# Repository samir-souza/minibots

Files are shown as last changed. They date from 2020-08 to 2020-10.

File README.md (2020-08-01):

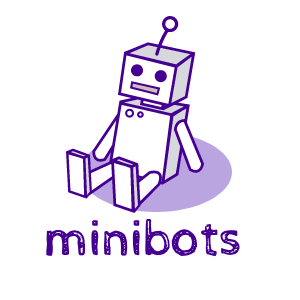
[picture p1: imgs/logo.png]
<br> 

**minibots** is an open source and open hardware platform for experimenting with autonomous bots, Machine Learning and Programming. You can download the code and the assets to create your own fleet of bots, using a 3D printer and some basic electronic components. It is based on the ESP8266 uController, but you can modify it and use any uController you want. 
 
<br><br> 

<p align="center">
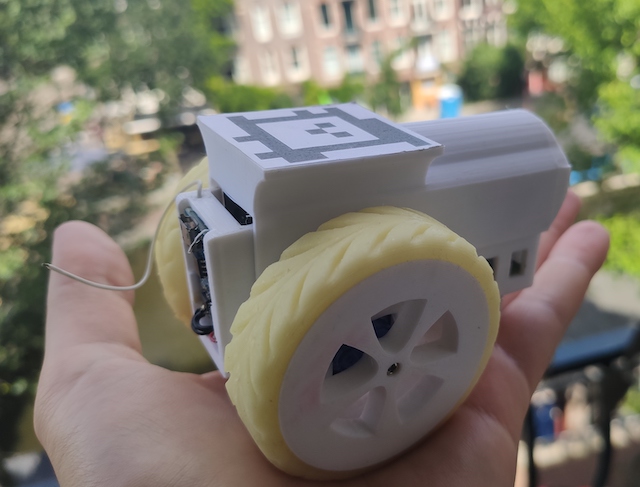
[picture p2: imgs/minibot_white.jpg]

</p>

## Smart City with minibots
In this repo you will find a demo of a Smart City simulation. The idea of this demo is to use **minibots** to 
represent cars moving around on the streets of a city. There are a few places around the track like: houses, gas stations, buildings, etc.
The cars are going from on place to another, simulating a rush hour and generting traffic jams. The targets are selected randomly, and
each car automatically selects the next random target as soon as it gets to the current target place. The controller will try to 
re-route the cars to alternative paths to alleviate the traffic. You can also make the things worse by manually adding some 
obstacles to the streets, like: dogs, pedestriang, etc.
Also, there is a special marker that you can put close to a place. It will bias the next target selected by the first car that finishes the current path.  

<p align="center">
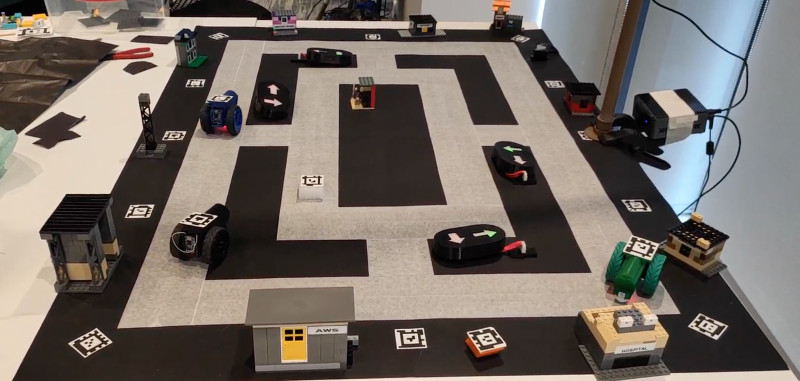
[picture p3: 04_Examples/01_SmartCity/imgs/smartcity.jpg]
 
</p> 

[Click here for more details about this demo](04_Examples/01_SmartCity)

## Components

A Minibot is composed by three modules: 1) the 3D printed parts and a few other parts; 2) the bot Printed Circuit Board (PCB); and 3) the firmware;

### 3D Models
In the first module [3D Models](01_3DModels) you will find the STL files and the FreeCAD projects used to build this project. Just follow the instructions on the module page "[3D Models](01_3DModels)" to get the files and print them.
### Bot PCB
In the second module [Bot PCB](02_BotPCB) you will find instructions about how to create the Printed Circuit Board for your Minibot. Also, you'll find the [Gerber files](https://en.wikipedia.org/wiki/Gerber_format), required for manufacturing the PCB and the components list.
### Firmware
In the third module [Firmware](03_BotFirmware) you will find the binary images and a Dockerfile that you can use to hack and customize the firmware of your Minibot. The firmware is for the uController ESP8266 and is based on Nodemcu LUA: https://nodemcu.readthedocs.io/en/master/. So, after installing the Nodemcu firmware you can customize the Lua scripts to adapt your Minibot to any project.

## Assembling
Click on [ASSEMBLING](ASSEMBLING.md) to see the instructions of how to create your own Minibot from scratch.

# License
The 3D Models and the PCB projects are released in Creative Commons Attribution-ShareAlike 4.0 License and the source code available in this repository is licensed under the GNU General Public License v3.0.

----
<div>Logo created by <a href="https://www.designevo.com/logo-maker/" title="Free Online Logo Maker">DesignEvo logo maker</a></div>

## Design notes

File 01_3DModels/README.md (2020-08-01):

## 3D Printing some parts for your Minibot

Here you will find all the parts you need to print in order to assembly your Minibot. Print the followint itens and prepare the [Printed Circuit Board - PCB](/02_BotPCB) to assemble your Minibot:

 - [Chassis](stl/01_Chassis.stl)
 - [Wheel (x2)](stl/02_Wheel.stl)
 - [Cover Shell](stl/21_MinibotShell.stl)
 - PCB Cover: Depending on the size of your servo (yes, it varies a lot from vendor to vendor), choose: [Big](stl/04_PCBCoverBig.stl) or [Small](stl/05_PCBCoverNormal.stl)

<table>
  <tr>
    <td align="center">Wheels</td>
    <td align="center">PCB with servos</td>
    <td align="center">Chassis cover</td>
    <td align="center">Wheels installed</td>
  </tr>
  <tr>
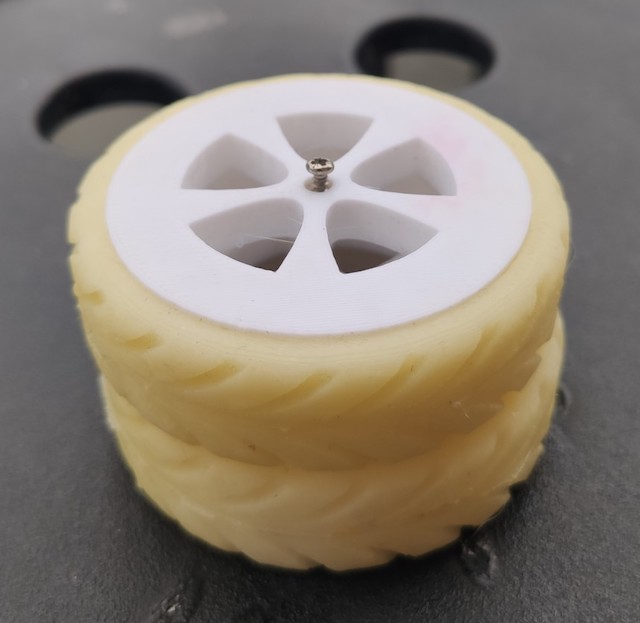
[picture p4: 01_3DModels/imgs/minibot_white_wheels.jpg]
    <td align="center"></td>
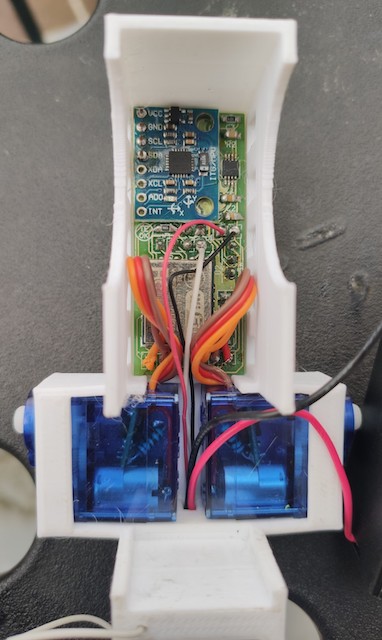
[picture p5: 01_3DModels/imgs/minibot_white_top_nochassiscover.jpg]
    <td align="center"></td>
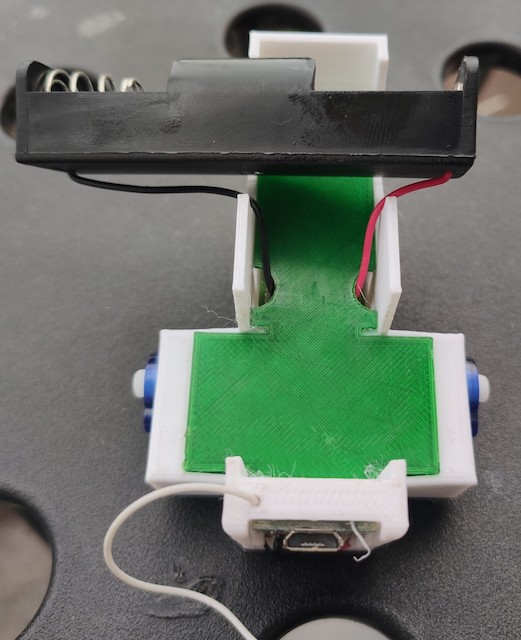
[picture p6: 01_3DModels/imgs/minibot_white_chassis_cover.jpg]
    <td align="center"></td>
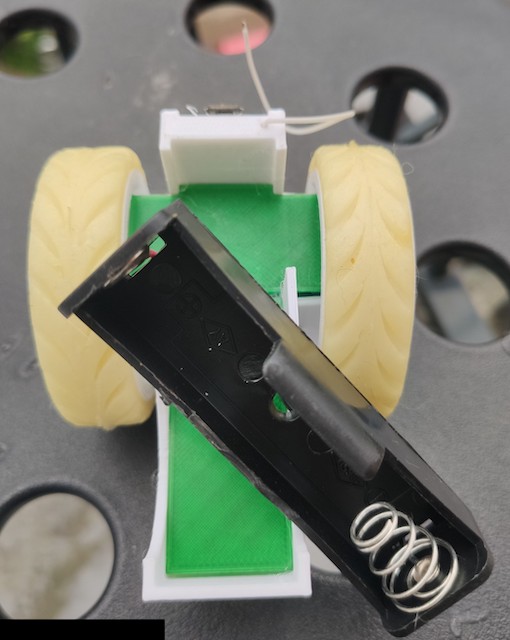
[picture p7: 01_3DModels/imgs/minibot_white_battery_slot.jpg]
    <td align="center"></td>    
  </tr>
  <tr>
    <td align="center">Without shell - battery slot</td>
    <td align="center">Top vision with shell</td>
    <td align="center">Rear view - battery recharger</td>
    <td align="center">Bottom view</td>
  </tr>
  <tr>
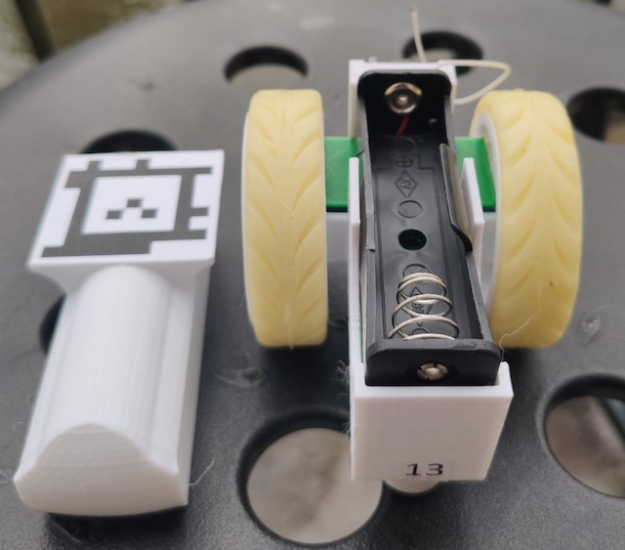
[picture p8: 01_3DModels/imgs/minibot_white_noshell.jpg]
    <td align="center"></td>    
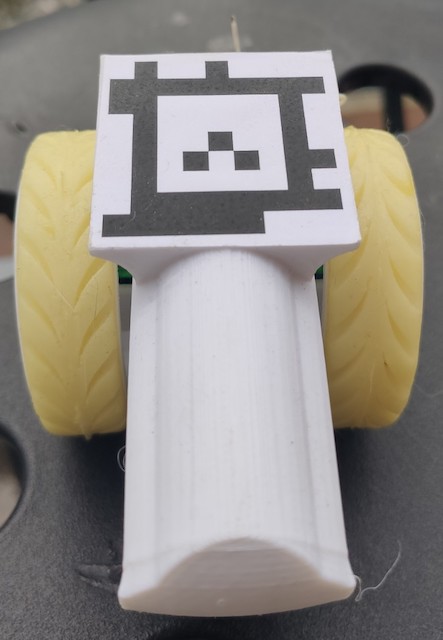
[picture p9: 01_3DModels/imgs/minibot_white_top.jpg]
    <td align="center"></td>
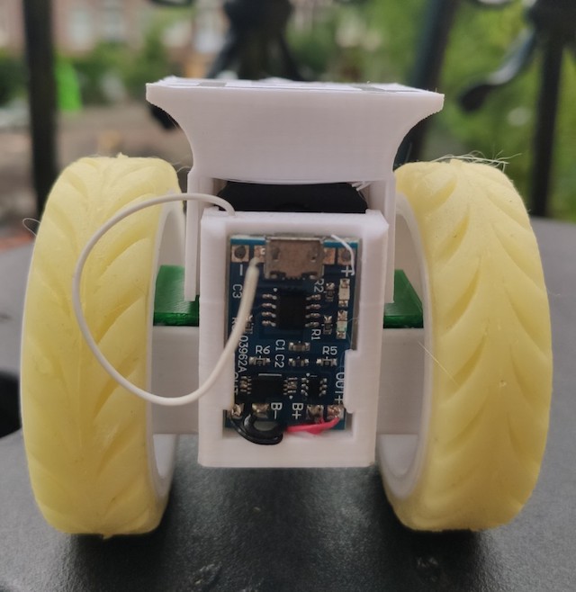
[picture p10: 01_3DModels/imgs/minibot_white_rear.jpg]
    <td align="center"></td>
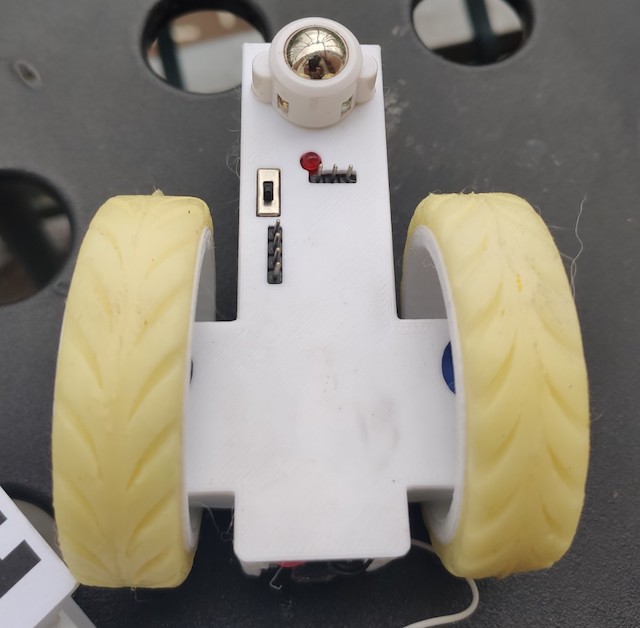
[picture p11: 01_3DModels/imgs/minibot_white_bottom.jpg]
    <td align="center"></td>
  </tr>
</table>

## Preparing the tyres
You can make tyres for your Minibot with Silicon and Cornstarch! :) Yeah, that's it. To do that, you just need to 3D print the mold:
 - [Mold part A](stl/32_TyreModePartA.stl)
 - [Mold part B](stl/33_TyreModldPartB.stl)
 
Then you just need to prepare the silicon the way it is explained here in this video: https://www.youtube.com/watch?v=u9VzjrzLDiE&pbjreload=101

Put the silicone in both parts of the mold, close it tightly and wait for ~2hs before opening it. Keep in mind the the cure time for this formula is something like 24hs. So, don't stretch or try to put it in the wheel before that time. IMO you achieve better by letting the tyres to cure for 48hs.

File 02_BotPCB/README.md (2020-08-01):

## Preparing the PCB

Minibots is based on a very popular and cheap uController, the ESP8266. So, the PCB is basically this uController connected to two servos (controlled by PWM) and other elements, like the classic accelerometer+gyroscope MPU6050, external pins, control LED, etc.

The PCB was created with KiCad **v4.0.2+dfsg1-stable** and you can see the KiCad project in this directory. The Gerber files can also be found in this dir. In order to manufacture a new PCB for you Minibot, you can use the Gerber files. If you never created a PCB before, you can use some online services that you just upload the Gerber files, pay for the boards and you then receive the boards at your home. The project is very simple. It has just one layer and you can make tracks with **copper 2Oz**.

<table>
  <tr>
    <td>PCB Layout</td>
    <td>Connections</td>
    <td>Top</td>
    <td>Bottom</td>
  </tr>
  <tr>
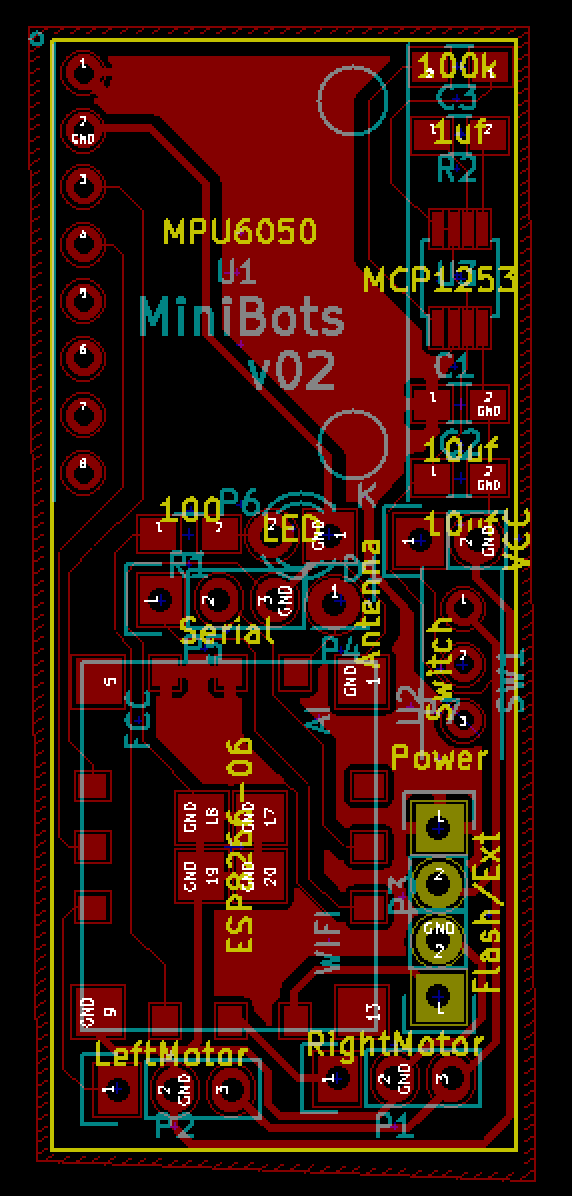
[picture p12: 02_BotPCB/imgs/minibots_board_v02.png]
    <td></td>
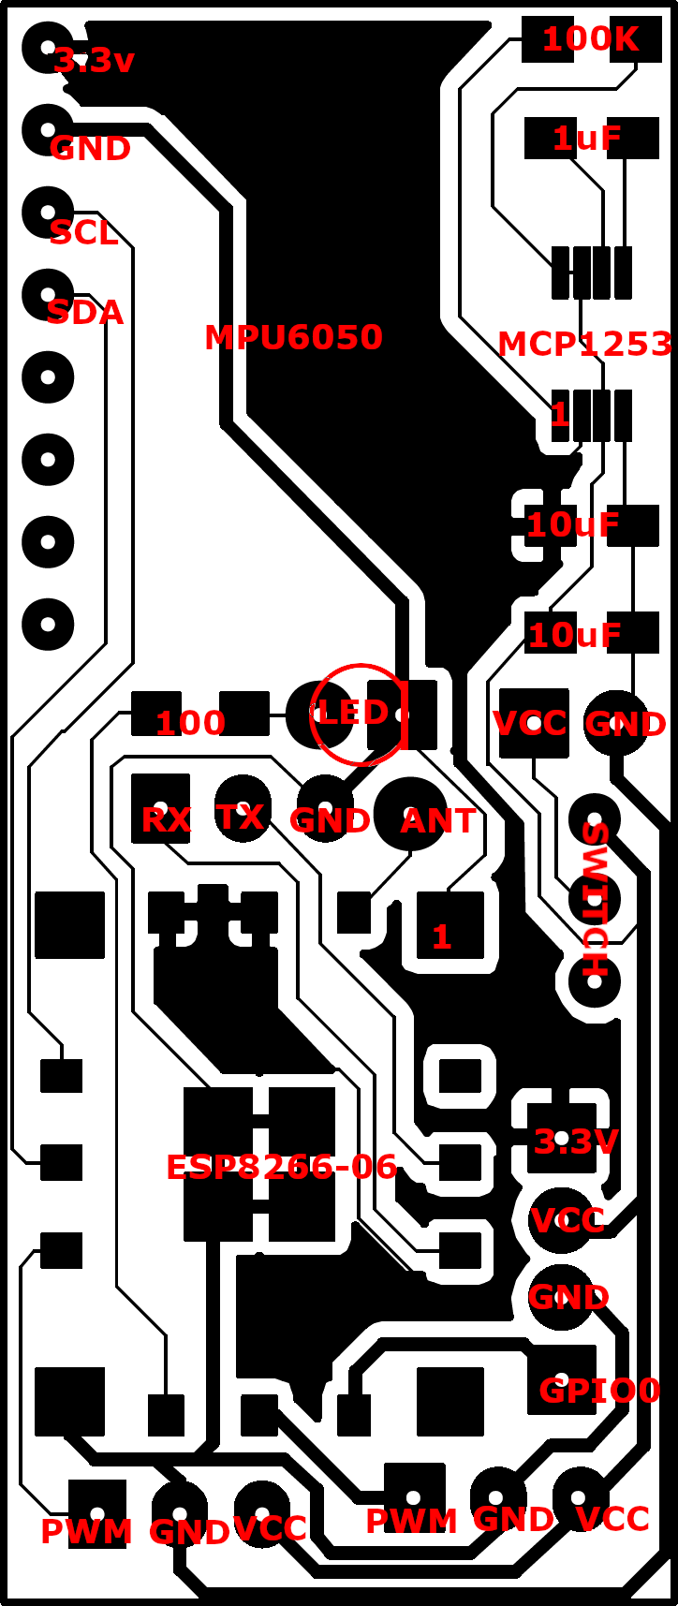
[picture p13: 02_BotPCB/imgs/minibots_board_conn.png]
    <td></td>
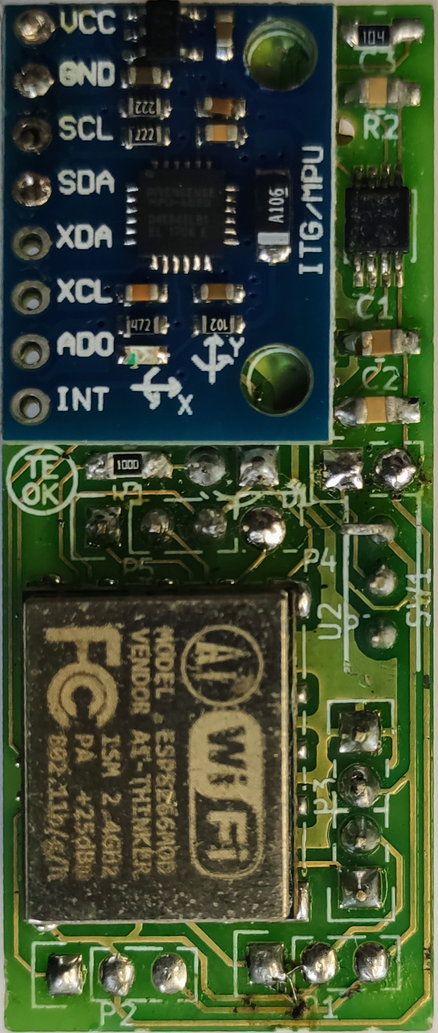
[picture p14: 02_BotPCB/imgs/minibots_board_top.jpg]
    <td></td>
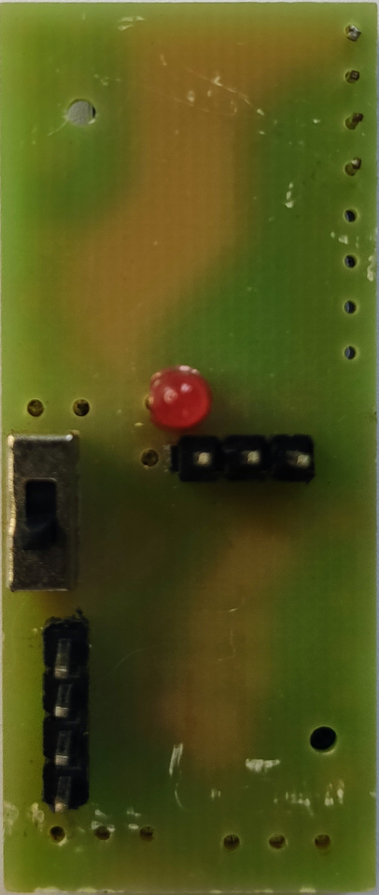
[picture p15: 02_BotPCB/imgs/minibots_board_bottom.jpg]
    <td></td>
  </tr>
</table>

As you can see above, the layout is very simple and the list of components (BOM) is:
 - D1: LED-3MM
 - P1: Pin_Header_Straight_1x03 ; LeftServo (Micro Servo 9g SG90 with 360o hack)
 - P2: Pin_Header_Straight_1x03 ; RightServo (Micro Servo 9g SG90 with 360o hack)
 - P4: Pin_Header_Straight_1x01 ; Antenna
 - P5: Pin_Header_Straight_1x03 ; Serial
 - SW1: MiniSlideSwitch ; [Switch specs](imgs/mini_switch.jpg)
 - U1: MPU6050 ; MPU6050
 - C1,C2: C_0805_HandSoldering ; 10uf
 - C3: C_0805_HandSoldering ; 1uf
 - R2: R_0805_HandSoldering ; 100k
 - U3: MSOP-8_3x3mm_Pitch0.65mm ; MCP1253
 - R1: R_0805_HandSoldering ; 100
 - P6: Pin_Header_Straight_1x02 ; VCC
 - P7: Pin_Header_Straight_1x02 ; Power
 - P3: Pin_Header_Straight_1x02 ; Flash/Ext
 - U2: ESP8266-06
 
 ### Considerations
 You need to have some soldering skills to put all the components on the board. The uController requires an SMD soldering station, but the rest of the components can be soldered by just using a normal iron.
 
 **Micro Servo 9g SG90** is a 180 degrees servo. You need to hack it to transform it into a continuous servo (360 degrees). There are tons of tutorials on the Internet teaching how to do that. Here it is an example: https://rookieelectronics.com/servohack/
 
 **MCP1253** is a power pump, it improves the battery energy utilization and also works as a power regulation. It's mandatory to keep the correct voltage (3.3v) all the time to the uController. It also works as a power isolation, given the servos are connected directly to the battery and the rest of the circuit is feed by the power pump.
 
 **ESP8266** package 04 was used in the original project, but this packaging was discontinued, so, in v02 (this version) the package 06 was used. It is easier to find on the Internet but it is more difficult to be soldered, given it requires a Rework station (SMD soldering machine with hot air).
 
 **SMD** is important to keep the size of the board in general. You can see that all the resistors and capacitors are **SMD 0805**.

 Bottom view of the Minibot after finishing the assembly in the 3D printed Chassis:  
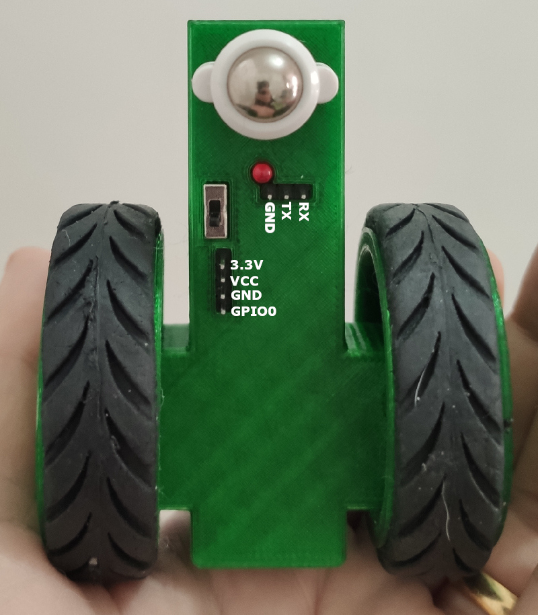
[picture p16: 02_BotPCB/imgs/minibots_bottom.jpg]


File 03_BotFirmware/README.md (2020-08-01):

## Preparing the uController with the Minibot firmware

### Esptool

First, you need to get and install **esptool** from: https://github.com/espressif/esptool  

### FLashing the device
You will find the compiled firmware and the compiled LFS in this dir. So, if you don't need to modify the source code, just use the instruction bellow to flash and configure your Minibot.

Then, get the code:
```bash
git clone https://github.com/samir-souza/minibots
cd minibots/03_BotFirmware
```

Take a look on the directory **bin**. You will see the file: **lfs.img** and the dir **firmware**. The first is the Lua LFS image and the second the uController firmware (ESP8266). To flash the ESP8266 do:
```bash
PORT=<REPLACE THIS WITH THE CORRECT "ESP USB SERIAL PORT" STRING> # i.e: MAC: /dev/cu.usbserial-A700abYF
BAUD=115200

# First let's clean the flash
esptool.py --port $PORT -b $BAUD erase_flash

# Then, write the new one
esptool.py --port $PORT -b $BAUD write_flash  -fm qio 0x00000 bin/firmware/0x00000.bin 0x10000 bin/firmware/0x10000.bin
```

### Load the Lua image+files and configure the bot
  - Get **ESPlorer** (https://esp8266.ru/esplorer/) to finish the configuration of the device. 
  - Turn the device on and open ESPlorer. 
  - Then upload the Lua image to the device (there is a button on ESPlorer called upload): **bin/lua.img**
  - On the **ESPlorer** terminal, run the following Lua command: node.flashreload("lfs.img")
     - It will load LFS to the device
  - Then, upload the following files: lua/config.lua lua/init.lua lua/main.lua
  - Edit the file lua/config.lua on the device and update the **WIFI** and **BACKEND SERVER** config
  - That's it! :)

## Compiling the Firmware
If you need to customize the LFS, there is a Docker container available. After editing the lua files in the **lua/LFS** dir, just follow these instructions to get a new version of the **lfs.img**.

Get the code, build the docker image and run it:
```bash
git clone https://github.com/samir-souza/minibots
cd minibots/03_BotFirmware
docker build -t minibots-firmware:1.0 Container/

### Modify the files in lua/LFS, then
docker run -it --rm -v $PWD/bin:/out -v $PWD/lua/LFS:/in  minibots-firmware:1.0
```

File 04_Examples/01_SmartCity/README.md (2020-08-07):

## SmartCity Example
The idea of this project is to simulate a minimalist (smart) city. People go around by car from one place to another during the rush hour. Traffic jams are inevitable. With the help of a Smart City, the drivers can change/optimize the routing, on-the-fly, based on "what the city sees and notifies to each car". 

So, with the use of a webcam, the city keeps "looking all the time" to the cars, pedestrians, obstacles, the streets, etc. A backend (written in C++ for performance reasons) process the video streaming from the camera and applies a set of rules to understand the current scenario and infer a better state for the city. This backend is the Smart City controller. It communicates to all the cars and the traffic lights trough UDP. All the elements share the same network.

<p align="center">
   
</p>

Each car, pedestrian, obstacle and place has an [Apriltag](https://april.eecs.umich.edu/software/apriltag). Apriltags are powerful visual markers used for experimenting with robotics and augmented reality. By processing the Apriltags, the backend identifies the position and orientation of all detected elements in the scene. These coordinates are then used to compute improvements in the routing.

The city has a representation of the track as a connected graph. For the path planning, A*. Both graph and path planner algorithms were implemented in an external library called [PowerGine](https://github.com/samir-souza/powergine).

For this project, a tripod with a Raspbery pi4 camera support was created. You can make your own tripod by PVC tubes and just one 3D printed part, as you can see in the picture bellow: 
<p align="center">
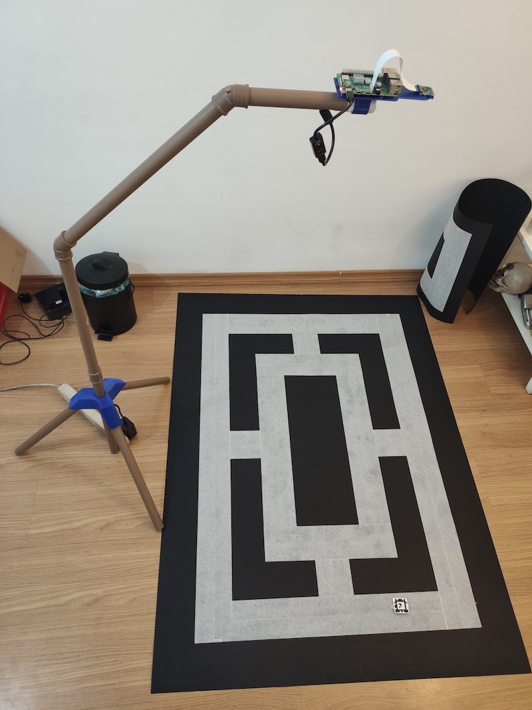
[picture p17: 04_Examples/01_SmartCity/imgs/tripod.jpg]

</p>

This project was created as a Proof of concept for the Minibots and was presented at the Builders Fair at re:Invent 2019. A special thanks to **Hugo Rozestraten** (hugorozestraten) that worked hard for many days and nights to make this project happen. Also, thanks to Edzon Sanchez (edzon) and Juan Mestre (juanmestre) that helped us to present this project to hundreds of people.

### How the Backend works

<p align="center">
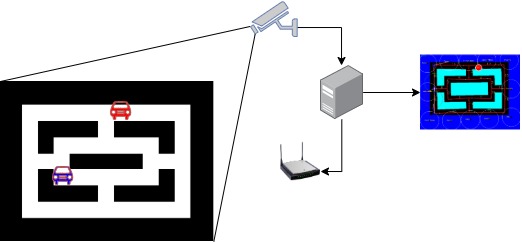
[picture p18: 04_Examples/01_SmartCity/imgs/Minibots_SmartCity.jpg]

</p>

Each captured frame is processed by the backend in a simple computer like a raspberry pi 4. After processing all the elements from a given frame, the Backend updates the map. A Map in this context is the spacial representation of the elements and their current state. This map is updated after each frame is processed. There is a visual debugger integrated with the Backend. It uses OpenCV to render the current state of the map in a screen. Here it is an example of this debugger showing:

<p align="center">
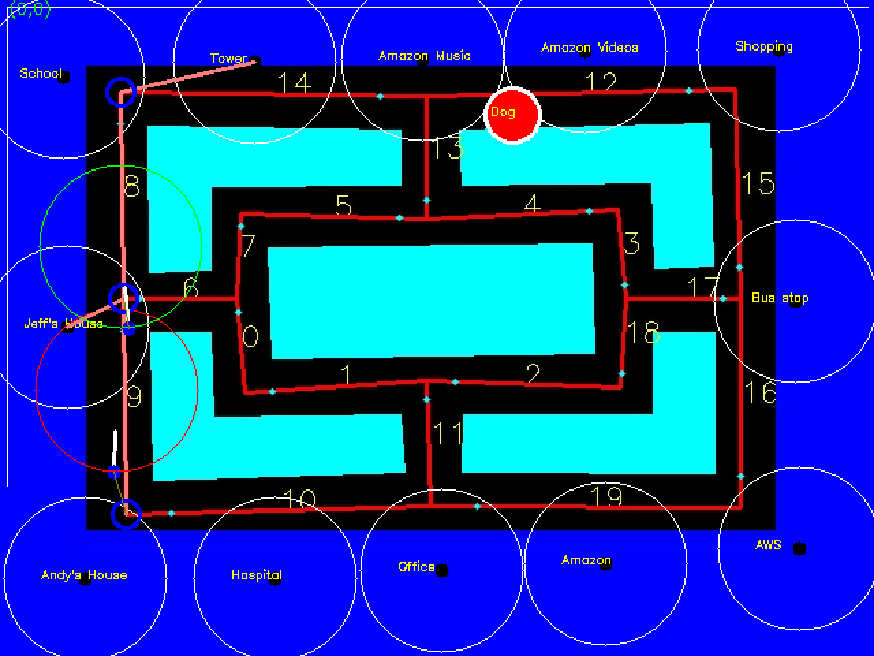
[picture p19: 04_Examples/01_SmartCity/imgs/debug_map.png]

</p>

#### Path planning
When the city detects that there is a better path for a given routing, it replans the path and then send this information to the bots. The bots in this demo are just following all the commands sent by the backend. In a real life scenario, this notification could be a message sent by the city to the driver and this particular driver then can use that info to take a decision.

### Compiling from Source
Please use this [Dockerfile](Container/Dockerfile) as a reference for building the backend from source. You'll notice that this project requires a few libraries:
 - [Powergine](https://github.com/samir-souza/powergine): A minimalist game engine for experimentation. We'll use the graph and path planner (A*) moduler from that lib
 - [Apriltag](https://github.com/AprilRobotics/apriltag.git): A library for parsing markers that represent the orientation and position of moving objects
 - [OpenCV](https://github.com/opencv/opencv.git): The classic Computer Vision lib

# Running the backend (requires a webcam)
./minibots -p

### Simulator
If you want to experiment with the algorithms that you can use in this city, you can use the Simulator provided by this project.

The simulator produces a similar output as a camera, positioned on top of the track, would create. With this Simulator you can debug and also experiment different controllers. Maybe Reinforcement Learning?

Click on the image bellow to watch a video that shows the simulator (at the left side) and the debugger of the backend (at the right side).
<p align="center">
  
</p>

The Simulator is a python 3 Script that uses [Pygame](http://pygame.org/) as the graphic renderer. Take a look at the dir: [Bot Simulator](BotSimulator) for more details.

It requires a few libraries and you can install them by running:
```bash
pip3 install pygame==2.0.0.dev6
pip3 install numpy
pip3 install opencv-python
```

If you want to try the simulator, you need to ask the backend not to look for a webcam and instead prepare a UDP server to receive the frames from the simulator.
```bash
# In the backend build dir
./minibots -p -s localhost:9991
```

Then in another terminal (tab?)
```bash
# In the simulator dir
python3 main.py
```

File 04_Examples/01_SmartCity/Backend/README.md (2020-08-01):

## Build from source

mkdir build && cd build. 
cmake ..  
make. 

## Create the path graph from the track
ln -s ../assets/config.yaml .  
./trackBuilder -i ../assets/track_test.png  

## Start the simulation
./minibots.

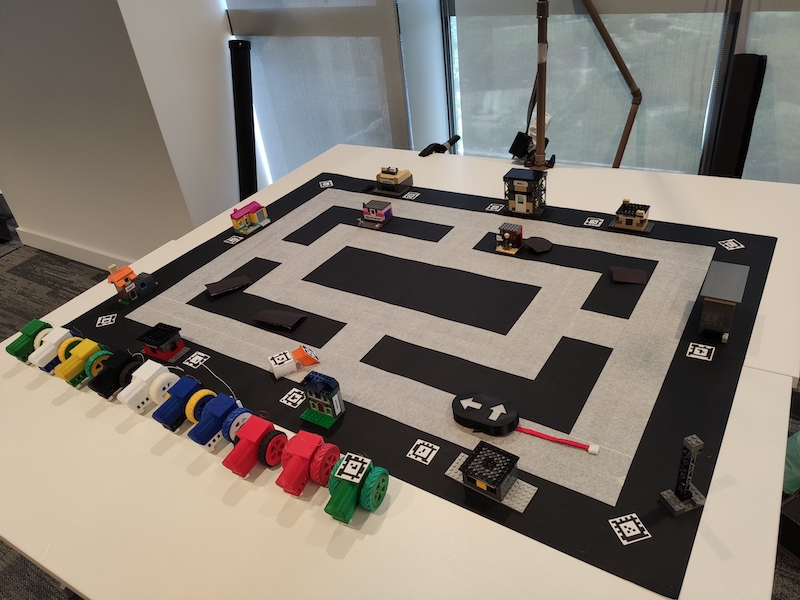
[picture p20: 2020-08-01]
04_Examples/01_SmartCity/imgs/track.jpg

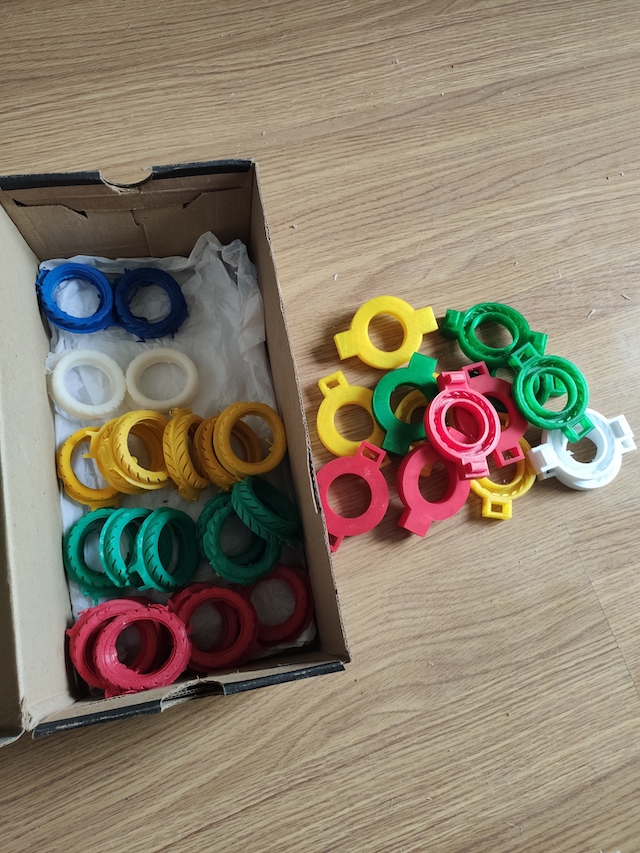
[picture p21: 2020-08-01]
04_Examples/01_SmartCity/imgs/tyres_n_molds.jpg

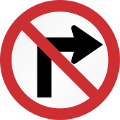
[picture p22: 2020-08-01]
04_Examples/01_SmartCity/BotSimulator/assets/traffic_sign_right_turn_prohibited.png

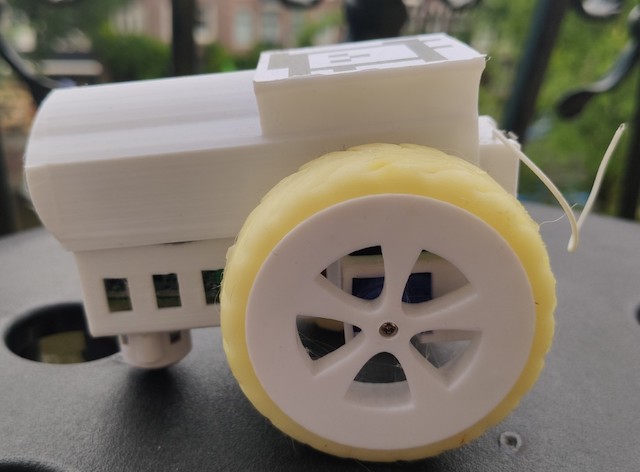
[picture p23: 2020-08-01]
imgs/minibot_white_side.jpg

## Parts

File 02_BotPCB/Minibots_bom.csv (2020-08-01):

Id | Designator | Package | Quantity | Designation | Supplier and ref
1 | D1 | LED-3MM | 1 | LED
2 | P1 | Pin_Header_Straight_1x03 | 1 | LeftMotor
3 | P2 | Pin_Header_Straight_1x03 | 1 | RightMotor
4 | P4 | Pin_Header_Straight_1x01 | 1 | Antenna
5 | P5 | Pin_Header_Straight_1x03 | 1 | Serial
6 | SW1 | MiniSlideSwitch | 1 | Switch
7 | U1 | MPU6050 | 1 | MPU6050
8 | C1,C2 | C_0805_HandSoldering | 2 | 10uf
9 | C3 | C_0805_HandSoldering | 1 | 1uf
10 | R2 | R_0805_HandSoldering | 1 | 100k
11 | U3 | MSOP-8_3x3mm_Pitch0.65mm | 1 | MCP1253
12 | R1 | R_0805_HandSoldering | 1 | 100
13 | P6 | Pin_Header_Straight_1x02 | 1 | VCC
14 | P7 | Pin_Header_Straight_1x02 | 1 | Power
15 | P3 | Pin_Header_Straight_1x02 | 1 | Flash/Ext
16 | U2 | ESP-06 | 1 | ESP8266-06

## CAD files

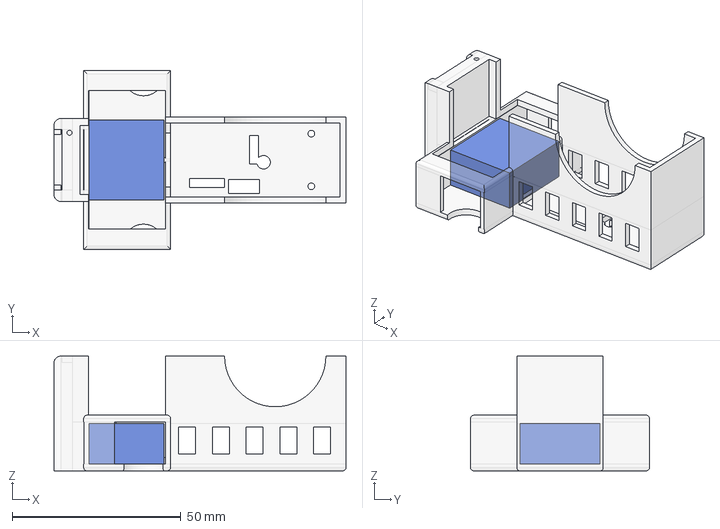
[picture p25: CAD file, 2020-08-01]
01_3DModels/01_Minibot.FCStd
86.5 x 53.0 x 34.0 mm
01_Chassis

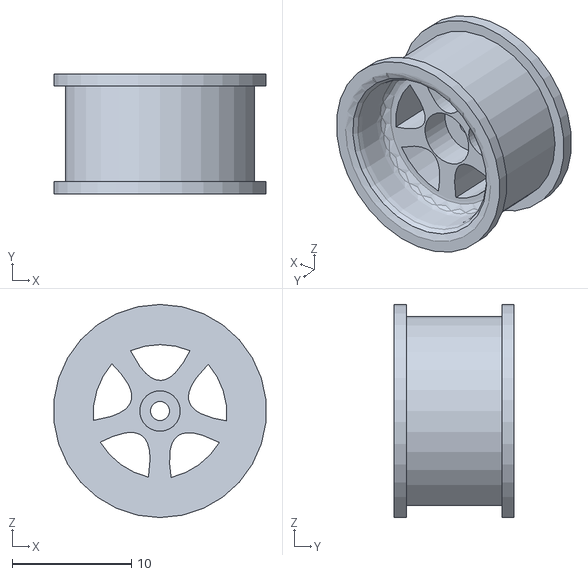
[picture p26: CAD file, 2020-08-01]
01_3DModels/stl/03_FrontWheel.stl
17.8 x 10.1 x 17.9

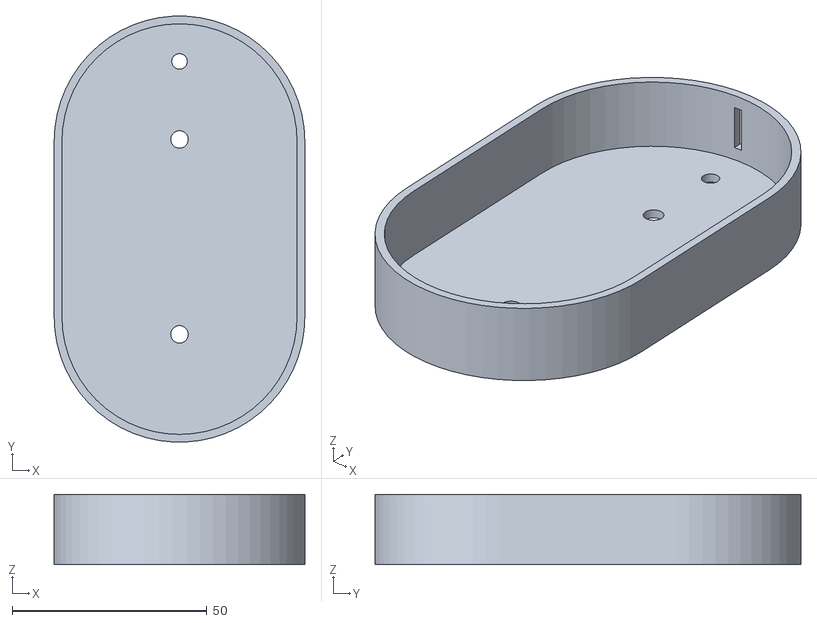
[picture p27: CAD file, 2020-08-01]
04_Examples/01_SmartCity/TrafficLight/3DModels/65_TrafficLightCaseBottom.stl
64.3 x 109.3 x 18.0

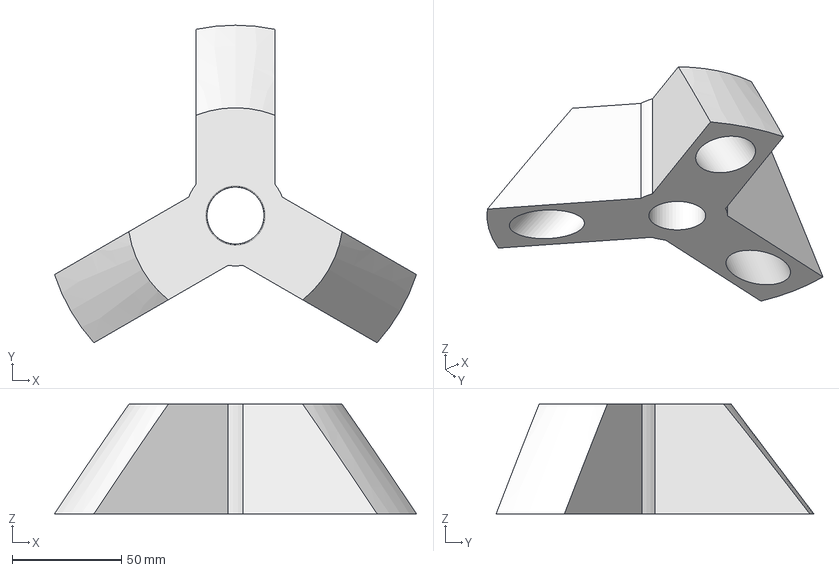
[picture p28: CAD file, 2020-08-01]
01_3DModels/04_CameraTripod.FCStd
165.4 x 145.1 x 50.1 mm

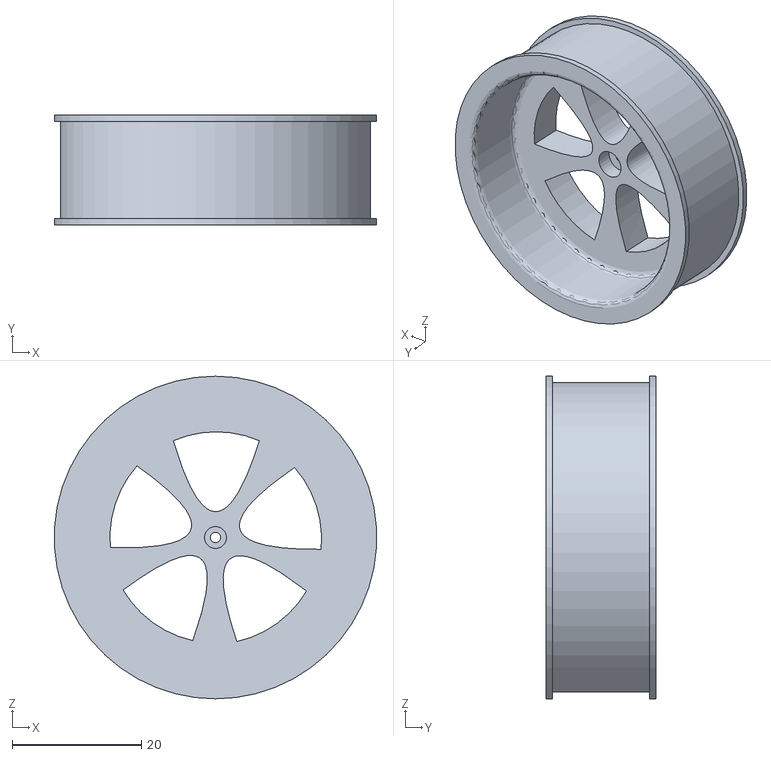
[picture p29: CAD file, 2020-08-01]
01_3DModels/stl/02_Wheel.stl
49.9 x 17.0 x 50.0

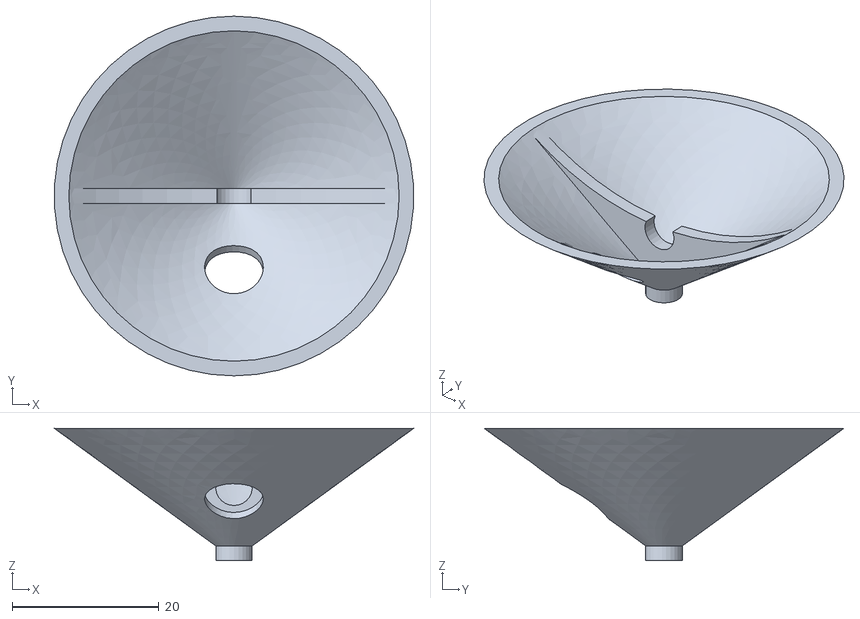
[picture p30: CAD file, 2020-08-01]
04_Examples/01_SmartCity/TrafficLight/3DModels/63_LedSupport.stl
48.9 x 49.0 x 18.0

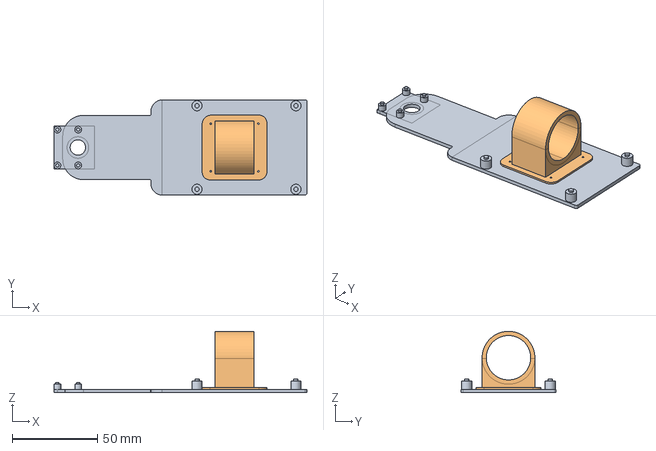
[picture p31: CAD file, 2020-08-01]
01_3DModels/05_CameraSupport.FCStd
148.4 x 56.0 x 36.0 mm
51_RaspCamSupport
52_RaspCamSupportFixer

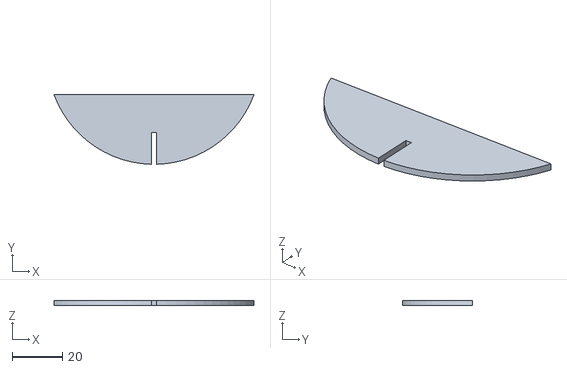
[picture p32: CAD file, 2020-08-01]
04_Examples/01_SmartCity/TrafficLight/3DModels/62_TrafficLightPoleBase.stl
80.0 x 27.8 x 2.00

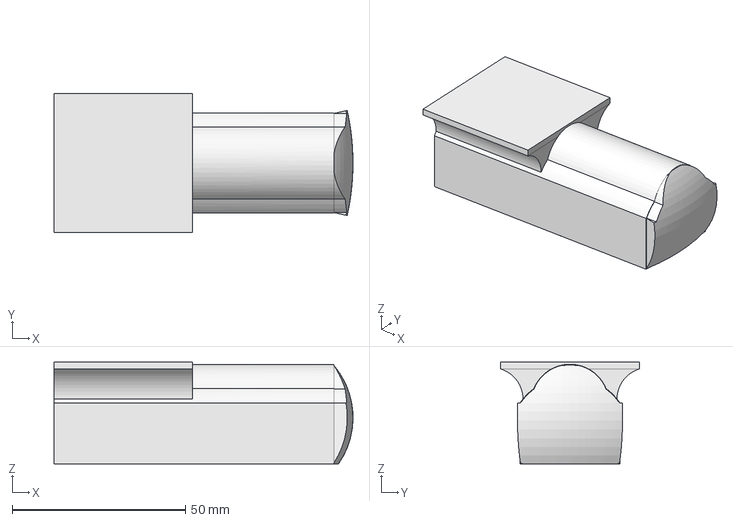
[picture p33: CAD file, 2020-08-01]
01_3DModels/02_MinibotShell.FCStd
86.2 x 40.0 x 29.4 mm

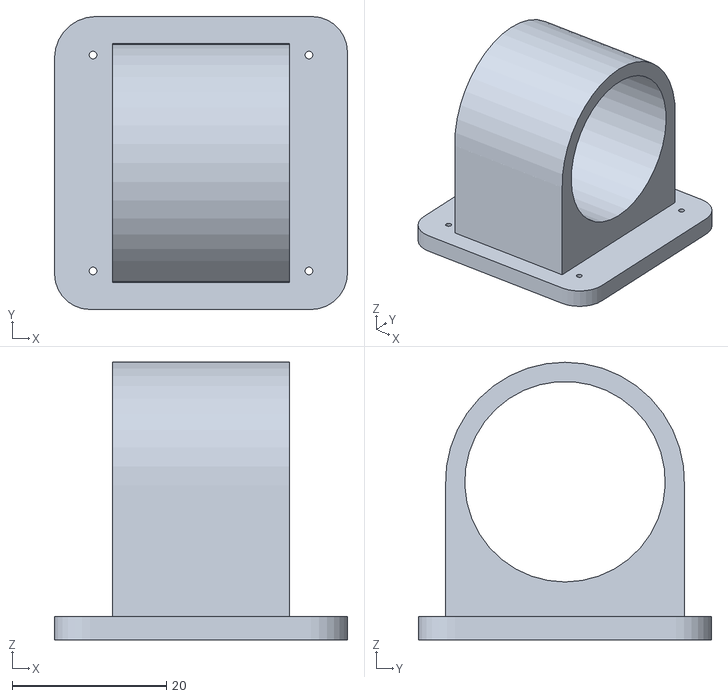
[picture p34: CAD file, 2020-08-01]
01_3DModels/stl/52_RaspCamSupportFixer.stl
38.0 x 38.0 x 36.0

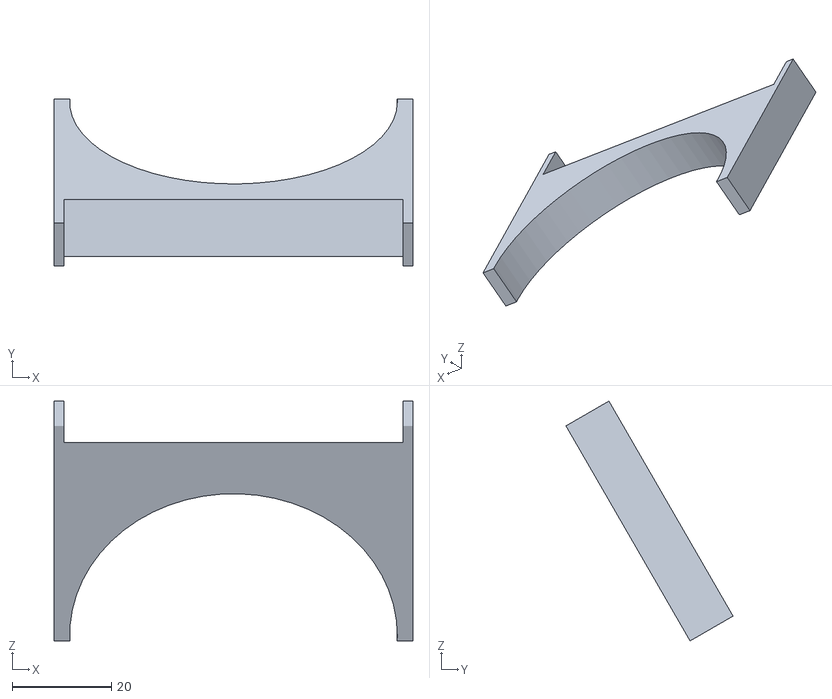
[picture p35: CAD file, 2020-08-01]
04_Examples/01_SmartCity/TrafficLight/3DModels/66_TrafficLightSupport.stl
72.3 x 33.7 x 48.3

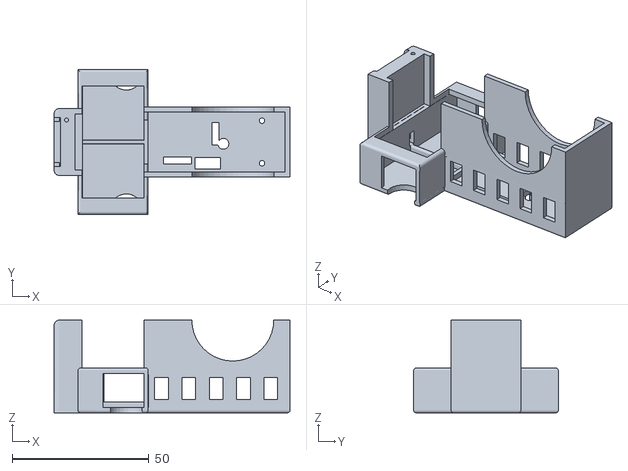
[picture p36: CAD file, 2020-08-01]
01_3DModels/stl/01_Chassis.stl
86.4 x 53.0 x 34.0

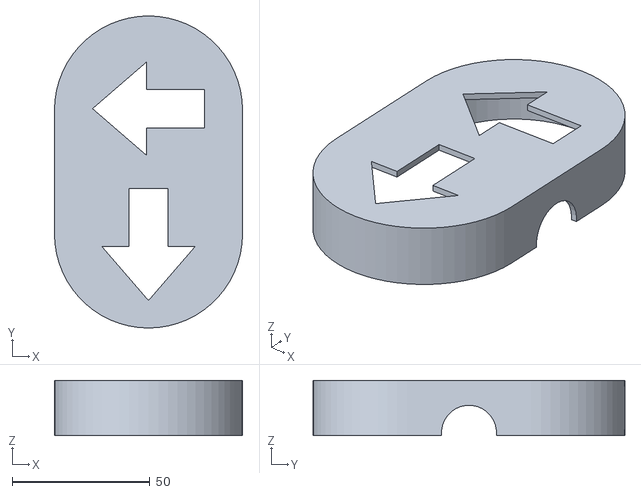
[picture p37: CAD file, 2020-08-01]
04_Examples/01_SmartCity/TrafficLight/3DModels/64_TrafficLightCaseTop.stl
68.3 x 113.3 x 20.0

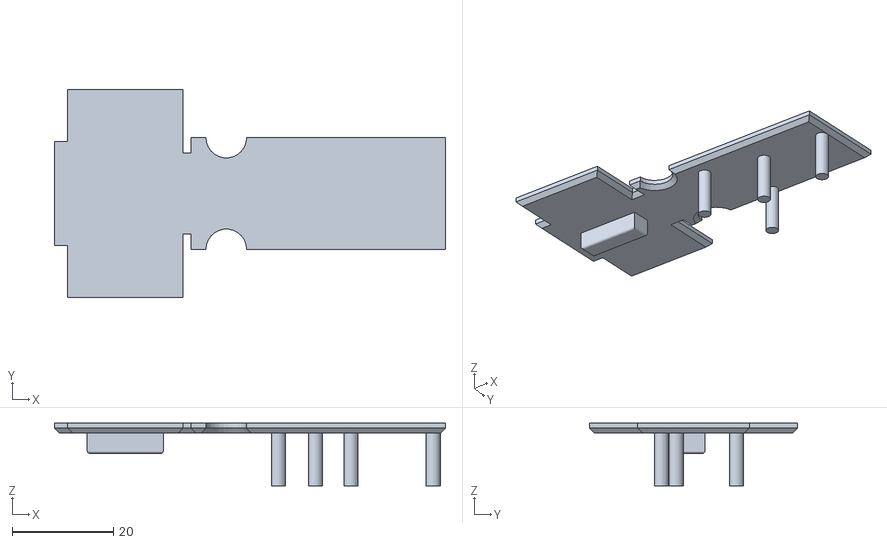
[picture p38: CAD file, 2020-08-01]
01_3DModels/stl/04_PCBCoverBig.stl
77.1 x 41.0 x 12.4

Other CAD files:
01_3DModels/stl/41_TripodSupport.stl
04_Examples/01_SmartCity/TrafficLight/3DModels/06_SmartCityTrafficLight.FCStd
01_3DModels/stl/51_RaspCamSupport.stl
04_Examples/01_SmartCity/TrafficLight/3DModels/61_TrafficLightPole.stl
01_3DModels/stl/05_PCBCoverNormal.stl
01_3DModels/stl/21_MinibotShell.stl
01_3DModels/stl/31_Tyre.stl
01_3DModels/stl/32_TyreModePartA.stl
01_3DModels/stl/33_TyreModldPartB.stl

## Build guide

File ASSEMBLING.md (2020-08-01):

## Assembling your Minibot

Before you start, make sure you already followed all the instructions in the three parts of this project and prepared the 3D printed parts and the PCB + installed the firmware.
  - [3D Models](/01_3DModels)
  - [Bot PCB](/02_BotPCB)
  - [Bot Firmware](/03_BotFirmware)

### Putting everything together

Let's start with a list of the components you need to complete this project:
  - [3D printed](/01_3DModels)
    - Two wheels
    - Chassis
    - PCB cover
    - Minibot Shell (cover)
  - [PCB](/02_BotPCB) (with all the components already soldered)
  - Two hacked servos (continuous rotation + use a cutting pliers to remove the flaps)
  - Two tyres
  - Caster wheel
  - Battery recharger module TP4056
  - Hard wire for the Antenna
  - 3.7v Single 18650 Battery Holder
  - Rechargeable 3.7v 18650 Battery
  
<table>
  <tr>
    <td align="center">Battery recharger TP4056</td>
    <td align="center">Caster wheel</td>
    <td align="center">3.7v Single 18650 Battery Holder</td>
 </tr>
 <tr>
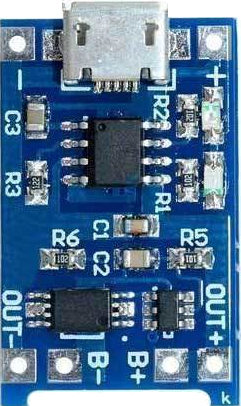
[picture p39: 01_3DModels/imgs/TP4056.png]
   <td align="center"></td>
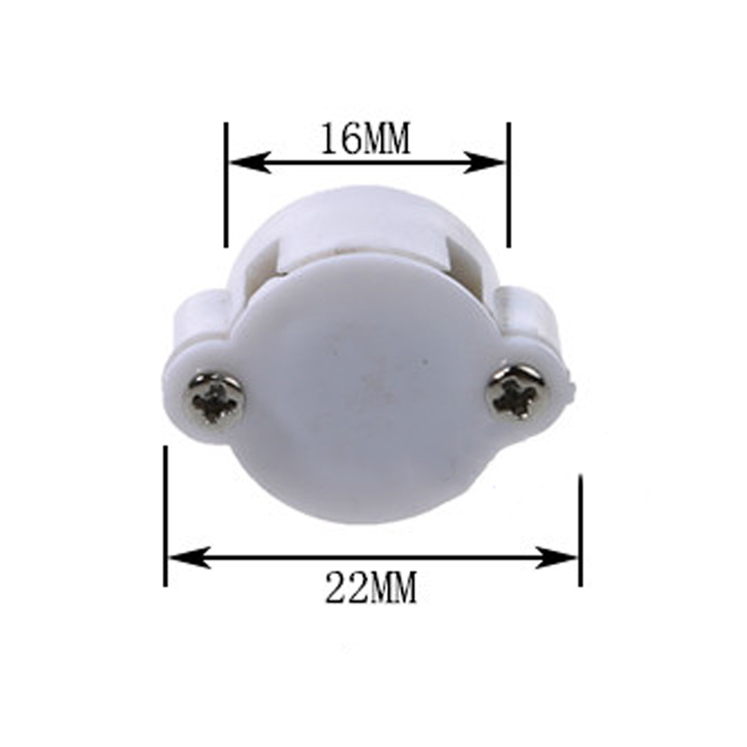
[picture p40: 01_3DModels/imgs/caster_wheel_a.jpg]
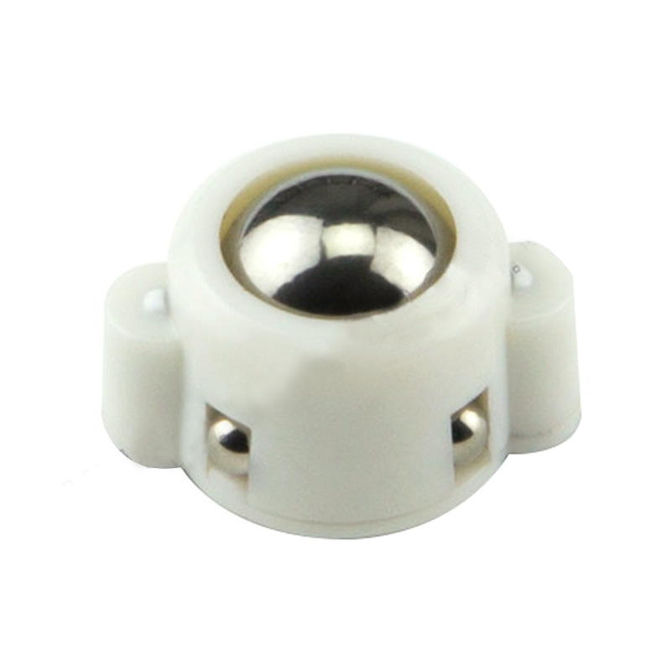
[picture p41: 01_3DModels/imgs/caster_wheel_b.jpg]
   <td align="center"></td>
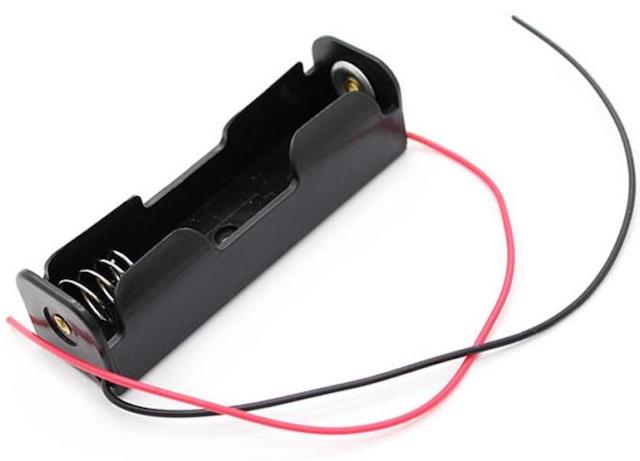
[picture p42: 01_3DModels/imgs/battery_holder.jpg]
   <td align="center"></td>
 </tr>
</table>

**TIP:** You need to cut the Servos wires to solder them to the PCB. Keep the wires to use them to connect the TP4056 to the PCB. Take a look on the Picture bellow called "PCB with servos" to have an idea of how to connect all the elements together.

<p align="center">
<table>
  <tr>
    <td align="center" colspan="4">Hacked Servo 9g S90</td>
 </tr>
 <tr>
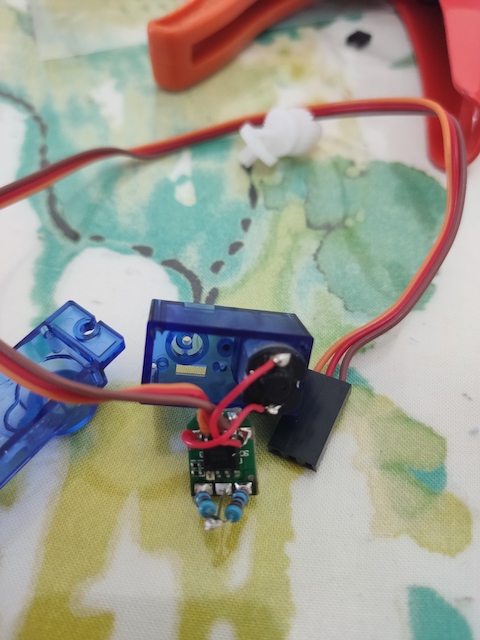
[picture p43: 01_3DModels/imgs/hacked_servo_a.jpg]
   <td align="center"></td>
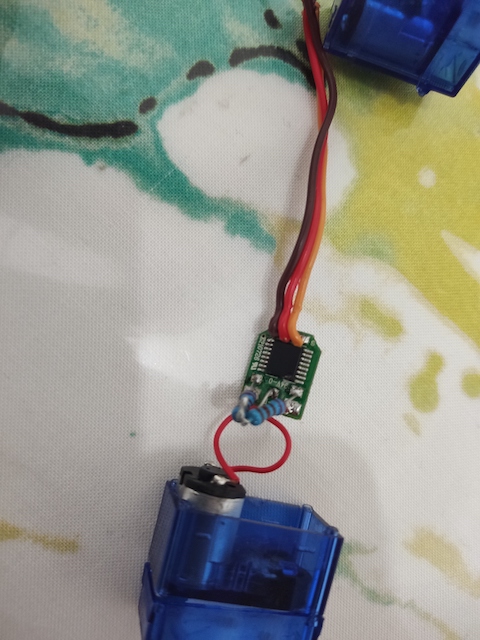
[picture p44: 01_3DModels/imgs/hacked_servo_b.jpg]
   <td align="center"></td>
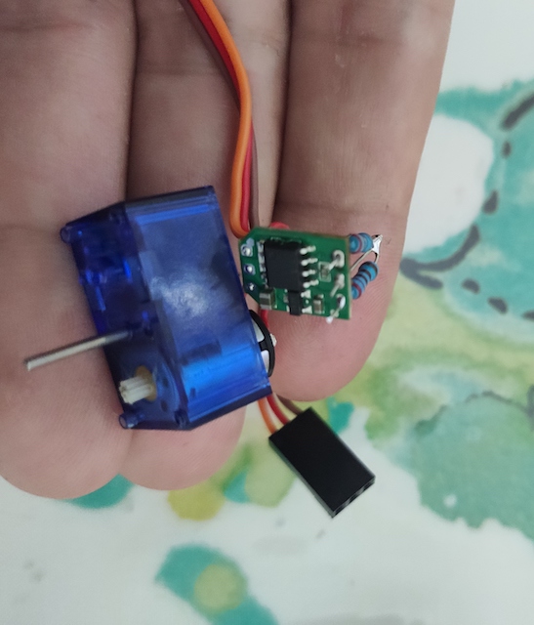
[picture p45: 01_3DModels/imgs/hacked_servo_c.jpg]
   <td align="center"></td>
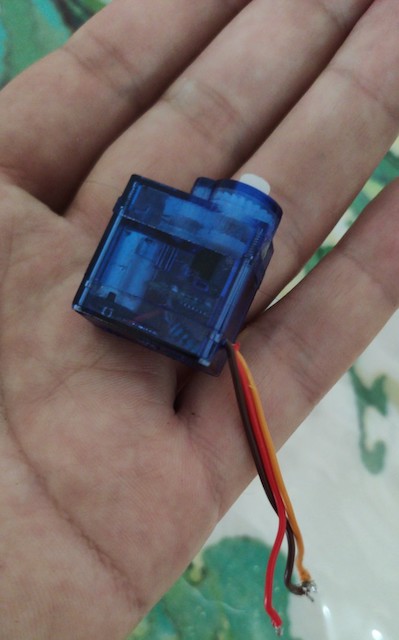
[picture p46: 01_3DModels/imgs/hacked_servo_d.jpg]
   <td align="center"></td>
 </tr>
</table>
</p>

**TIP:** *Micro Servo 9g SG90* is a 180 degrees servo. You need to hack it to transform it into a continuous servo (360 degrees). There are tons of tutorials on the Internet teaching how to do that. Here it is an example: https://rookieelectronics.com/servohack/

Alright! So, now that you have all the components, use the following diagram to guide you during the soldering/connecting:
<p align="center">
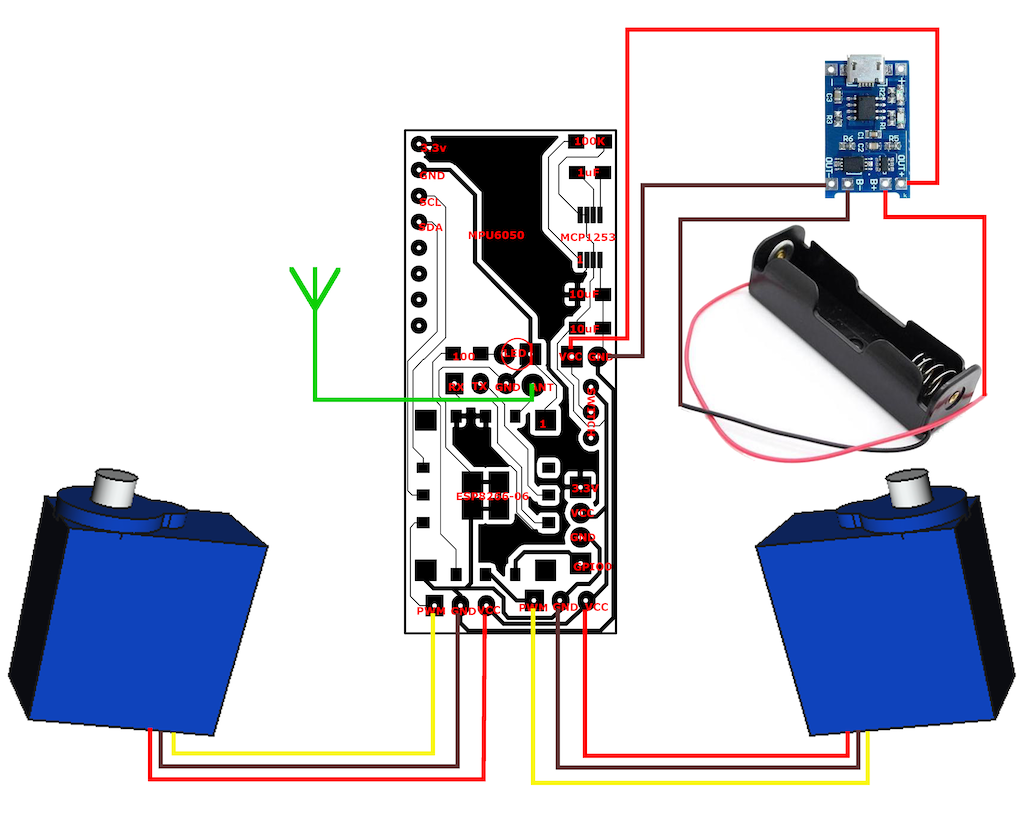
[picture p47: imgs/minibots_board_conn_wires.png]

</p>

**ATTENTION:** Before soldering the battery recharger and the battery holder, pass the wires through a (squared) hole in the chassis that goes from the servos area to the back of the Minibot. Then you can finish to install the servos and the PCB inside the chassis and put the PCB Cover. After that you can cut the wires to the right size, slide the battery recharger (TP4056) to the correct place (picture bellow) and finally you can solder the wires from the battery holder and the power connection to the recharger. Put a drop of hot glue at each side of the recharger to get a better fixation.

<p align="center">
<table>
  <tr>
    <td align="center">Wheels</td>
    <td align="center">PCB with servos</td>
    <td align="center">Chassis cover</td>
    <td align="center">Wheels installed</td>
  </tr>
  <tr>
    <td align="center"></td>
    <td align="center"></td>
    <td align="center"></td>
    <td align="center"></td>    
  </tr>
  <tr>
    <td align="center">Without shell - battery slot</td>
    <td align="center">Top vision with shell</td>
    <td align="center">Rear view - battery recharger</td>
    <td align="center">Bottom view</td>
  </tr>
  <tr>
    <td align="center"></td>    
    <td align="center"></td>
    <td align="center"></td>
    <td align="center"></td>
  </tr>
</table>
</p>

When attaching the wheels to the servos, just put a little preasure on it to fit it all the way. Then, use the screws that come with the servos to fix the wheels.

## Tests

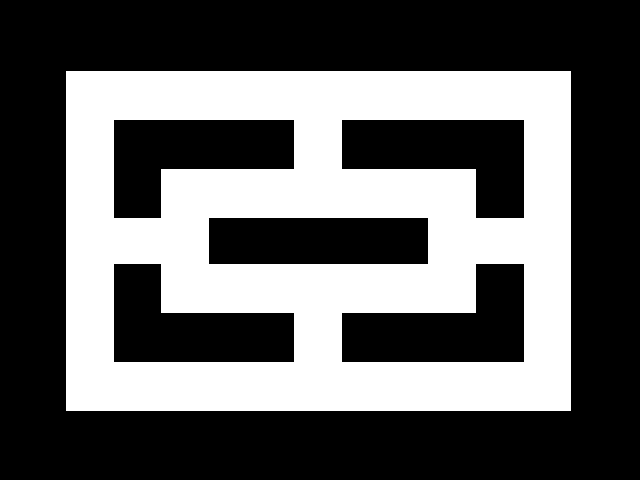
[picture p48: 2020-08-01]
04_Examples/01_SmartCity/Backend/assets/track_test.png

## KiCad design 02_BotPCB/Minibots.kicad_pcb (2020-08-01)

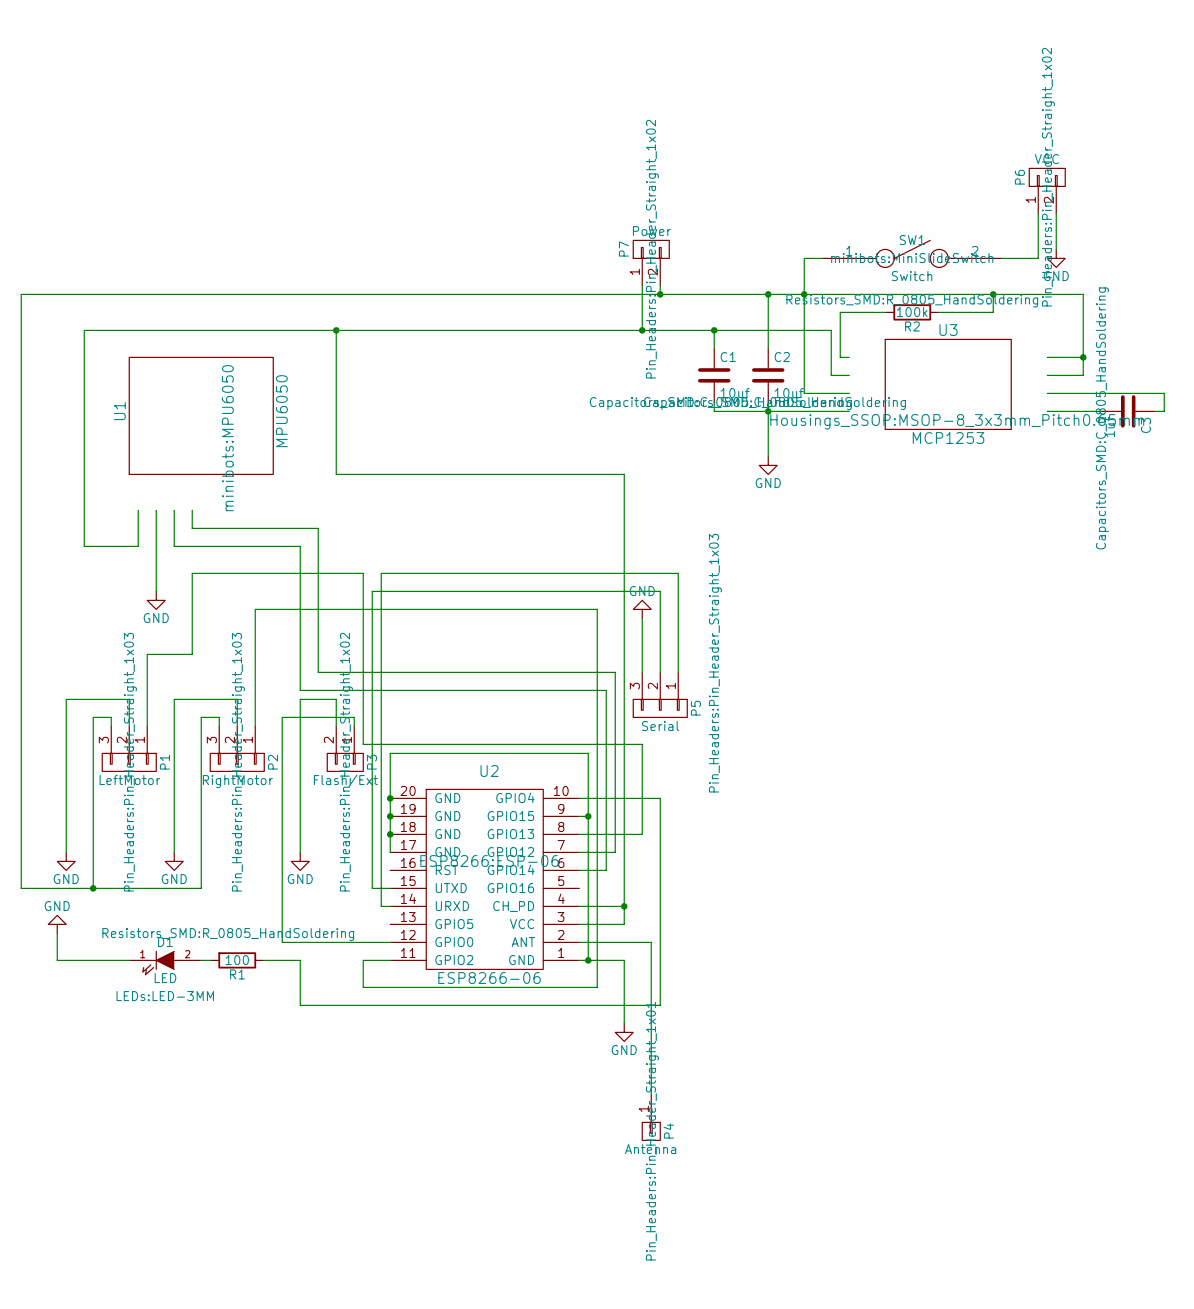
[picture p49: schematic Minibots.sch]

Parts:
C1, C2: 10uf; C_0805_HandSoldering
C3: 1uf; C_0805_HandSoldering
D1: LED; LED-3MM
P1: LeftMotor; Pin_Header_Straight_1x03
P2: RightMotor; Pin_Header_Straight_1x03
P3: Flash/Ext; Pin_Header_Straight_1x02
P4: Antenna; Pin_Header_Straight_1x01
P5: Serial; Pin_Header_Straight_1x03
P6: VCC; Pin_Header_Straight_1x02
P7: Power; Pin_Header_Straight_1x02
R1: 100; R_0805_HandSoldering
R2: 100k; R_0805_HandSoldering
SW1: Switch; MiniSlideSwitch
U1: MPU6050
U2: ESP8266-06; ESP-06
U3: MCP1253; MSOP-8_3x3mm_Pitch0.65mm

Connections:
GND: C1.2, C2.2, D1.1 (K), P1.2, P2.2, P3.2, P5.3, P6.2, U1.2 (GND), U2.1 (GND), U2.9 (GPIO15), U2.17 (GND), U2.18 (GND), U2.19 (GND), U2.20 (GND), U3.4 (GND)
unnamed: C1.1, P7.1, U1.1 (VCC), U2.3 (VCC), U2.4 (CH_PD), U3.2 (VOUT)
unnamed: C2.1, P1.3, P2.3, P7.2, R2.1, SW1.1, U3.3 (VIN), U3.7 (SHDN), U3.8 (SELECT)
unnamed: C3.1, U3.6 (C+)
unnamed: C3.2, U3.5 (C-)
unnamed: D1.2 (A), R1.2
unnamed: P1.1, U2.8 (GPIO13)
unnamed: P2.1, U2.11 (GPIO2)
unnamed: P3.1, U2.12 (GPIO0)
unnamed: P4.1, U2.2 (ANT)
unnamed: P5.1, U2.14 (URXD)
unnamed: P5.2, U2.15 (UTXD)
unnamed: P6.1, SW1.2
unnamed: R1.1, U2.10 (GPIO4)
unnamed: R2.2, U3.1 (PGOOD)
unnamed: U1.3 (SCL), U2.6 (GPIO14)
unnamed: U1.4 (SDA), U2.7 (GPIO12)

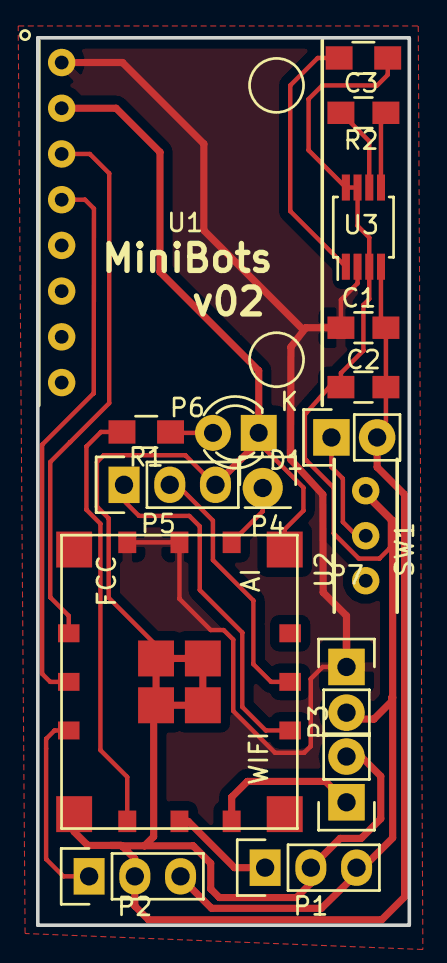
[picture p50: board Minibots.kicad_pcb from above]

Board: 2 copper layers, 20.6 x 49.3 mm, 17 parts (0 on the bottom side), 17 nets.

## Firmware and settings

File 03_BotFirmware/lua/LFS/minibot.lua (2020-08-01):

require 'class'
require 'mpu6050'
require 'wificontroller'
require 'vector'

MiniBot = class()
MiniBot.PI_2 = math.pi*2

function MiniBot:init(config)
    self.server_user = config.server_user
    self.server_pwd = config.server_pwd
    self.crypto_key = config.crypto_key
    self.bot_id = config.bot_id

    self.mpu_config = {
        scl_pin = 5,
        sda_pin = 6,
        bus = 0,
        dev_addr = 0x68
    }
    
    self.servo_left = { 
        pin = config.servo_left.pin
        
    }
    self.servo_right = { 
        pin = config.servo_right.pin
    }

    self.pos = Vector()
    self.cam_dir = Vector(1,0,0) -- top left corner is (0,0)
    self.seek = Vector()
    self.accel_world = {x=0, y=0, z=0}
    self.yaw = 0
    self.roll = 0
    self.pitch = 0
    self.voltage = adc.read(0)
    self.motion_status = 0

    -- server didn't accepted this bot yet
    self.active = false
    
    
    self.wifi = WifiController(config.wifi_ssid,config.wifi_pwd)
    self.wifi.got_ip_cb = function(t) self:main(t) end
    self.wifi.connected_cb = function(t) self:connected(t) end
    self.wifi.disconnected_cb = function(t) self:reconnect(t) end
        
    self.server = net.createUDPSocket()
    self.server_host = config.server_host
    self.server_port = config.server_port
    
    self.client = net.createUDPSocket()
    self.client_port = config.client_port
    
    self.client:on("receive", function(sck, data, port, ip) 
        self:on_receive(sck, data, port, ip) 
    end)
 
end

function MiniBot:start()
    self.sensors_timer = tmr.create()
    self.sensors_timer:register(250, tmr.ALARM_AUTO, function() self:read_sensors() end )
    
    self.sync_backend = tmr.create()
    self.sync_backend:register(250, tmr.ALARM_AUTO, function() self:send_telemetry() end )
    
    self.main_timer = tmr.create()
    self.main_timer:register(200, tmr.ALARM_AUTO, function() self:steering() end )
    
    self.wifi:start()
end

function MiniBot:send_telemetry()
    local msg = string.format("t;%d;%.03f;%.03f;%.03f;%.03f;%.03f;%.03f;%d;%d",
         tmr.now() / 1000.0, self.roll, self.pitch, self.yaw,
        self.accel_world.x, self.accel_world.y, self.accel_world.z,
        self.voltage, node.heap()
    )
    self:send_message(msg)

end

function MiniBot:get_delta_angle(angle1, angle2) -- in radians
    local delta = angle1 - angle2
    if math.abs(delta) > math.pi then
        delta = delta < 0 and delta+self.PI_2 or delta-self.PI_2
    end
    return delta
end

function MiniBot:read_sensors()
    local ts = tmr.now()
    --collectgarbage()
    self.voltage = adc.read(0)
    if self.mpu then
        -- 10825
        local fifo_count = self.mpu:get_fifo_count()
        
        if fifo_count > 42 then
            --32358
            local packet = self.mpu:get_fifo_bytes(42)
            -- 8664
            local ori = self.mpu:get_orientation(packet)
            -- 8664
            local gravity = self.mpu:get_gravity(ori)
            -- 8154
            self.yaw,self.pitch,self.roll = self.mpu:get_yaw_pitch_roll(ori,gravity)
            -- 881
            --local accel = self.mpu:get_accel(packet)
            -- 8533
            --self.accel_world = self.mpu:get_linear_accel_in_world(accel, ori) 
            -- 40790         
            self.mpu:reset_fifo()
            -- 35741
            --ts = tmr.now()
            
            --self.delta_yaw = self:get_delta_angle(self.yaw, self.previous_yaw)
        end

    end
    --print('read_sensors',(tmr.now()-ts)/1000)
end

function MiniBot:steering()
    local ts = tmr.now()

    local nextDir = self.seek - self.pos
    local distToTarget = nextDir:get_magnitude()
    
    -- TODO: Set threshold in config
    if distToTarget > 5 then -- we are far from the target, let's move
        --if self.new_seek == true then
        --    self.new_seek = false
            -- let's seek a target

            -- with this operation we get the angle between the bot dir
            -- and the desired target dir
            -- we need to minimize the target Angle.
        --    self.targetAngle = self.cam_dir:get_angle(nextDir)
            
            -- ok, since we have a angle shift of PI/2, lets adjust the angle
            -- based on curr yaw.
        --    self.targetAngle = self:get_delta_angle( self.yaw, -self.targetAngle )
        --end
        
        --local deltaAngle = self:get_delta_angle( self.yaw, self.targetAngle )
        --print(self.targetAngle, deltaAngle, self.yaw)
       local deltaAngle = nextDir:get_angle( self.cam_dir )
        --local deltaAngle = -self.cam_dir:get_angle(nextDir)
        
        
        
        --- RIGHT
        -- step1 : 0.116130
        -- step2 : 0.226470
        -- step3 : 0.301119
        -- step4 : 0.494105
        -- step5 : 0.634162
        --- LEFT
        -- step1 : 0.129935
        -- step2 : 0.280129
        -- step3 : 0.330724
        -- step4 : 0.466449  
        -- step5 : 0.629485
        local absDeltaAngle = math.abs(deltaAngle)
        local servo_left_duty, servo_right_duty
        
        if absDeltaAngle > 0.30 then -- step1
            local step = absDeltaAngle > math.pi/2 and self.speed2 or self.speed1
            if deltaAngle >= 0 then
                self.motion_status = 1 -- turn left
                servo_left_duty = self.servo_left.b - step
                servo_right_duty = self.servo_right.f - step
            else
                self.motion_status = 2 -- tern right
                servo_left_duty = self.servo_left.f + step
                servo_right_duty = self.servo_right.b + step
            end
        else
            local step = distToTarget > 30 and self.speed3 or self.speed1
            self.motion_status = 3 -- go straight
            servo_left_duty = self.servo_left.f + step
            servo_right_duty = self.servo_right.f - step
        end

        pwm2.set_duty( self.servo_left.pin, servo_left_duty )
        pwm2.set_duty( self.servo_right.pin, servo_right_duty )

        pwm2.start()
    else
        self.motion_status = 0
        pwm2.stop()
    end

end
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

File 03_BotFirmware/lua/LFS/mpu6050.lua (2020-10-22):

require 'class'
require 'vector'
require 'quaternion'

MPU6050 = class()

function MPU6050:__constants()
    self.GYRO_CONFIG = 0x1B
    self.ACCEL_CONFIG = 0x1C
    self.PWR_MGMT_1 = 0x6B
    self.RA_USER_CTRL = 0x6A
    self.DMP_EN_BIT = 7
    self.USERCTRL_DMP_RESET_BIT = 3
    self.PWR1_DEVICE_RESET_BIT = 7
    self.PWR1_SLEEP_BIT = 6
    self.RA_INT_STATUS = 0x3A
    self.DMP_CONFIG_SIZE = 192

    self.RA_FIFO_COUNTH = 0x72
    self.RA_MOT_THR = 0x1F
    self.RA_ZRMOT_THR = 0x21
    self.RA_MOT_DUR = 0x20
    self.RA_ZRMOT_DUR = 0x22
    self.RA_XG_OFFS_TC = 0x00
    self.RA_YG_OFFS_TC = 0x01
    self.RA_ZG_OFFS_TC = 0x02
    self.XA_OFFS_H = 0x06
    self.YA_OFFS_H = 0x08
    self.ZA_OFFS_H = 0x0A
    self.XG_OFFS_USRH = 0x13
    self.YG_OFFS_USRH = 0x15
    self.ZG_OFFS_USRH = 0x17
    self.BANK_SEL = 0x6D
    self.MEM_R_W = 0x6F

    self.OTP_BNK_VLD_BIT = 0
    self.I2C_SLV0_ADDR = 0x25
    self.USERCTRL_I2C_MST_EN_BIT = 5
    self.USERCTRL_I2C_MST_RESET_BIT = 1
    self.USERCTRL_FIFO_RESET_BIT = 2
    self.USERCTRL_FIFO_EN_BIT = 6
    self.MEM_START_ADDR = 0x6E
    self.MPU6050_DMP_CODE_SIZE = 1929
    self.DMP_MEMORY_CHUNK_SIZE = 16
    self.ACCEL_XOUT_H = 0x3B

    self.GYRO_FS_250 = 0x00
    self.GYRO_FS_500 = 0x01
    self.GYRO_FS_1000 = 0x02
    self.GYRO_FS_2000 = 0x03

    self.DLPF_BW_42 = 0x03
    self.EXT_SYNC_TEMP_OUT_L = 0x1
    
    self.RA_INT_ENABLE = 0x38
    self.RA_SMPLRT_DIV = 0x19
    self.RA_DMP_CFG_1 = 0x70
    self.RA_DMP_CFG_2 = 0x71
    
    self.WHO_AM_I = 0x75
    self.MEAN_SENSORS_ITERATIONS = 1000
    self.RA_CONFIG = 0x1A
    self.RA_FIFO_R_W = 0x74
    self.initialized = false
end

function MPU6050:init(sda, scl, dev_addr, bus)
    if not i2c.setup(bus, sda, scl, i2c.SLOW) then
        print('Failed to intilialize MPU')
        return nil
    end
    self:__constants()
    self.dev_addr = dev_addr
    self.bus = bus

    print('Initializing MPU...')
    self:write_byte( self.GYRO_CONFIG, self.GYRO_FS_250) -- GYRO_CONFIG set Full scale range +/- 250 degree/C
    self:write_byte( self.ACCEL_CONFIG, 0x00) -- ACCEL_CONFIG set +/- 2g full scale
    self:write_byte( self.PWR_MGMT_1, 0x01) -- PWR_MGMT_1 0x00000001

    tmr.delay(3000000)
    if file.open("calibration.txt", "r") then
        print('Loading calibration from file')
        local data = file.read()
        file.close()
        t={}
        for c in string.gmatch(data, "%S+") do table.insert(t,c) end
        
        self:set_imu_offset(t[1],t[2],t[3], t[4],t[5],t[6])
        print('IMU offsets: ', self:get_imu_offset())
    else
        self:auto_calibrate()
    end
    
    tmr.delay(1000000)
    if not self:check() then
        print('IMU initialization failed..')
        
    elseif self:dmp_initialize() == 0 then
        print('MPU6050 Initialized!')
        self.initialized = true
    else
        print('Something went wrong')
        tmr.delay(5000000)
        return nil
    end
    
    
end

function MPU6050:is_initialized()
    return self.initialized
end

function MPU6050:set_slave_address(num, address)
    if num > 3 then
        return self:write_byte(self.I2C_SLV0_ADDR + num*3, address)
    end
end


function MPU6050:write_memory_block(data, bank, address, verify)
    local dataSize = #data
    if dataSize < 1 then
        print('There is no data to write')
        return false
    end
    local pivot = 0
    while dataSize > 0 do
        local chunkSize = self.DMP_MEMORY_CHUNK_SIZE
        if dataSize < chunkSize then chunkSize = dataSize end
        
        local buffer = {}
        for i=1,chunkSize do buffer[i] = data[pivot+i] end

        self:set_memory_bank(bank)
        self:set_memory_start_address(address)
        self:write_bytes(self.MEM_R_W, buffer)
       
        -- verify data if needed
        if verify then
            self:set_memory_bank(bank)
            self:set_memory_start_address(address)
            -- I2Cdev::readBytes(devAddr, MPU6050_RA_MEM_R_W, chunkSize, verifyBuffer);
            verifyBuffer = self:read_bytes(self.MEM_R_W, chunkSize)
            
            for j=1,chunkSize do 
                if buffer[j] ~= verifyBuffer[j] then 
                    print("Block write verification error, bank ",bank,", address ",address, " index ", j)
                    return false
                end 
            end
        end
        
        dataSize = dataSize - chunkSize
        address = address + chunkSize
        pivot = pivot + chunkSize
        collectgarbage()
    end
    print('Data loaded and verified successfully! :)')
    return true

end

function MPU6050:write_dmp_configuration_set(data)
    local dataSize = #data
    if dataSize < 1 then
        print('There is no data to write')
        return false
    end
    local pivot = 1
    local success = false
    while pivot < dataSize do
        local bank = data[pivot]
        local address = data[pivot+1]
        local chunkSize = data[pivot+2]
        pivot = pivot + 2

        if chunkSize > 0 then
            local buffer = {}
            print('Loading ', chunkSize, 'into bank', bank, 'address', address, 'pivot', pivot)
            for i=1,chunkSize do buffer[i] = data[pivot+i] end
            success = self:write_memory_block(buffer, bank, address, true)
            pivot = pivot + chunkSize + 1
        else
            -- special instruction
            -- NOTE: this kind of behavior (what and when to do certain things)
            -- is totally undocumented. This code is in here based on observed
            -- behavior only, and exactly why (or even whether) it has to be here
            -- is anybody's guess for now.
            local special = data[pivot+1]
            pivot = pivot + 2
            print( 'Special command, ', special)
            if special == 0x01 then
                -- enable DMP-related interrupts
                --I2Cdev::writeByte(devAddr, MPU6050_RA_INT_ENABLE, 0x32) -- single operation
                self:write_byte(self.RA_INT_ENABLE, 0x32)
                success = true;
            else
                -- unknown special command
                success = false
            end
        end
        if not success then break end
    end
    return success
end
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

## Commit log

2020-08-01 - All files
    [01_Chassis.stl, 01_Minibot.FCStd, 02_MinibotShell.FCStd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]
2020-08-01 - fixed a bug with the login message
    [minibot.lua]
2020-10-22 - fix quaternion reading
    [mpu6050.lua]

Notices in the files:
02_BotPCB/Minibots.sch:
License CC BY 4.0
